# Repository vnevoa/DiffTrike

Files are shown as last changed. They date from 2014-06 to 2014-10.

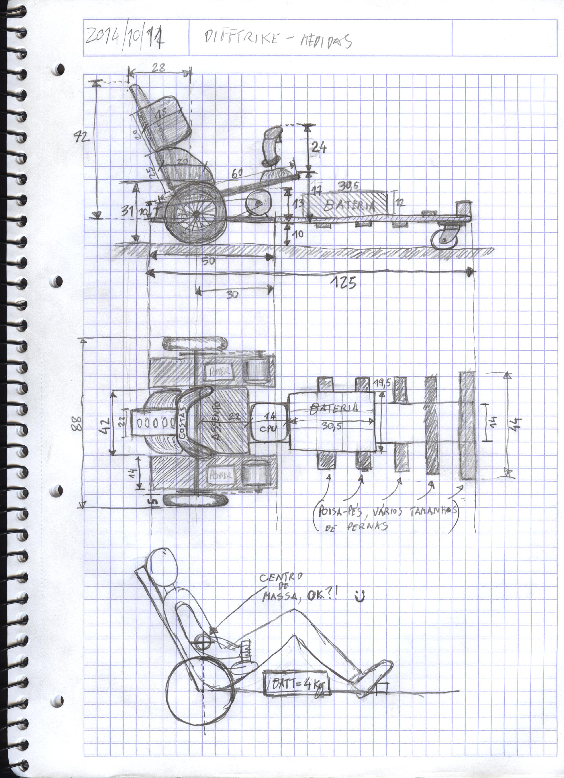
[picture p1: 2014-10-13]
Mechanical/MakerFaire Difftrike MarkIV dimensions.jpg

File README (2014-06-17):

The DiffTrike project attempts to develop the embedded control system
for a Differential Traction Hybrid Human-Electric Tricycle.

The project hosts one set of files for each hardware incarnation:
- MarkI: no files, was a purely analog solution.
- MarkII: Openmoko GTA02 controller + NJay's Homebrew Power bridges.
- MarkIII: Raspberry Pi controller + Devantech MD03 robotics power bridges.
- MarkIV: Raspberry Pi controller + NJay's Homebrew Power bridges & comms bridge.

The copyright licence of this Open Source project's files is the GNU GPL version 3.
Feel free to hack away, fork, or contribute. Just don't ask me for money for any reason whatsoever. :)

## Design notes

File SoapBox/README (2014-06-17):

This is the place for all the files that implement the SoapBox Mark IV proof-of-concept controller, in its fourth incarnation platform. Everything here is copied into the on-board controller of the Trike. 
Currently the chosen Hardware for this controller is a Raspberry Pi board, type A (use /dev/i2c-0 instead of /dev/i2c-1 on type B) plus a pair of NJay's Homebrew Power bridges.

The GNU/Linux distribution used as a basis for this controller is the Debian based "Raspbian" because it is the one suggested by the RasPi community.
You can download the latest card-flashable images from http://www.raspberrypi.org/downloads and flash them onto the SD-card by following these instructions: http://elinux.org/RPi_Easy_SD_Card_Setup

After flashing and booting it and running the built-in configuration wizard, just copy over the files to /home/pi/SoapBox/, open up a console (local or SSH) and run the install script by doing "chmod +x /home/pi/SoapBox/sbinstall.sh; sudo /home/pi/SoapBox/sbinstall.sh".

Project files and their function:
- "sbinstall.sh": the installation script for this software package into a Raspbian distro.
- "interfaces" corresponds to the /etc/network/interfaces linux configuration file.
- "soapbox.sh" is a SysV init script that launches and kills the controller application once it is installed in /etc/init.d/ and links produced with "update-rc.d soapbox.sh defaults".
- "sb.py": the control application itself, to be placed in /home/pi/SoapBox/.
- "sb_*.py": the custom modules necessary to the main application, also going into /home/pi/SoapBox/.

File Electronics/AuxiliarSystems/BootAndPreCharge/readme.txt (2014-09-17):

DiffTrike system boot and precharge auxiliar system.

Power is applied to the sub-systems by means of relays, such that power can be
enabled/disabled safely by the system controller or user.

To turn ON the trike there must be a procedure that ensures safetty, avoiding
unintended motor turn ON. And there must be a simple way for a human to quickly
turn power OFF in an emergency.

Power controllers such as motor controllers have big capacitance at the power
rails input. This capacitance needs to be charged in a controlled way to avoid
huge inrush currents which cause switch sparking and capacitor accelerated
ageing. It is the task of the precharger to slowly charge the capacitance until
it approaches the system voltage, and only then enable full power to the power
controller.

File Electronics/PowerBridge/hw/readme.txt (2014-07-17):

Here is the hardware design files for the DiffTrike h-bridge controller.
This is still work in progress, and the project is not yet totally decoupled
from my personal development environment, so you've been warned.

There are 4 boards in this project, developed with KiCAD:

 1) bridge-power
    The base board that holds the power switches (MOSFETs), DC-link capacitors,
    current sense resistors, fast current sens voltage comparator, 5V regulator
    and connectors for the controller and MOSFET driver boards.

 2) bridge-fet-drivers
    4 discreet MOSFET drivers, 2 for a N-channel and 2 for a P-channel, 24V
    power supply.

 3) bridge-ctrller
    Microcontroller and related support circuitry to control the bridge.

 4) bridge-ctrller-addon
    I2C isolation bridge, heatsink temperature sensing, motor temperature
    sensing support circuitry.

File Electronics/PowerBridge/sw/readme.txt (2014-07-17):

Here is the software for the DiffTrike h-bridge controller.
This is still work in progress, and the project is not yet totally decoupled
from my personal development environment, so you've been warned.

The software implements an I2C interface of 8 registers of 1 byte and controls
the 4 switches (currently MOSFETs) of an h-bridge by providing speed (PWM) and
reporting motor current, temperatures and bridge supply voltage.
Synchronous rectification is employed for improved efficiency over the simpler
assynchronous method.

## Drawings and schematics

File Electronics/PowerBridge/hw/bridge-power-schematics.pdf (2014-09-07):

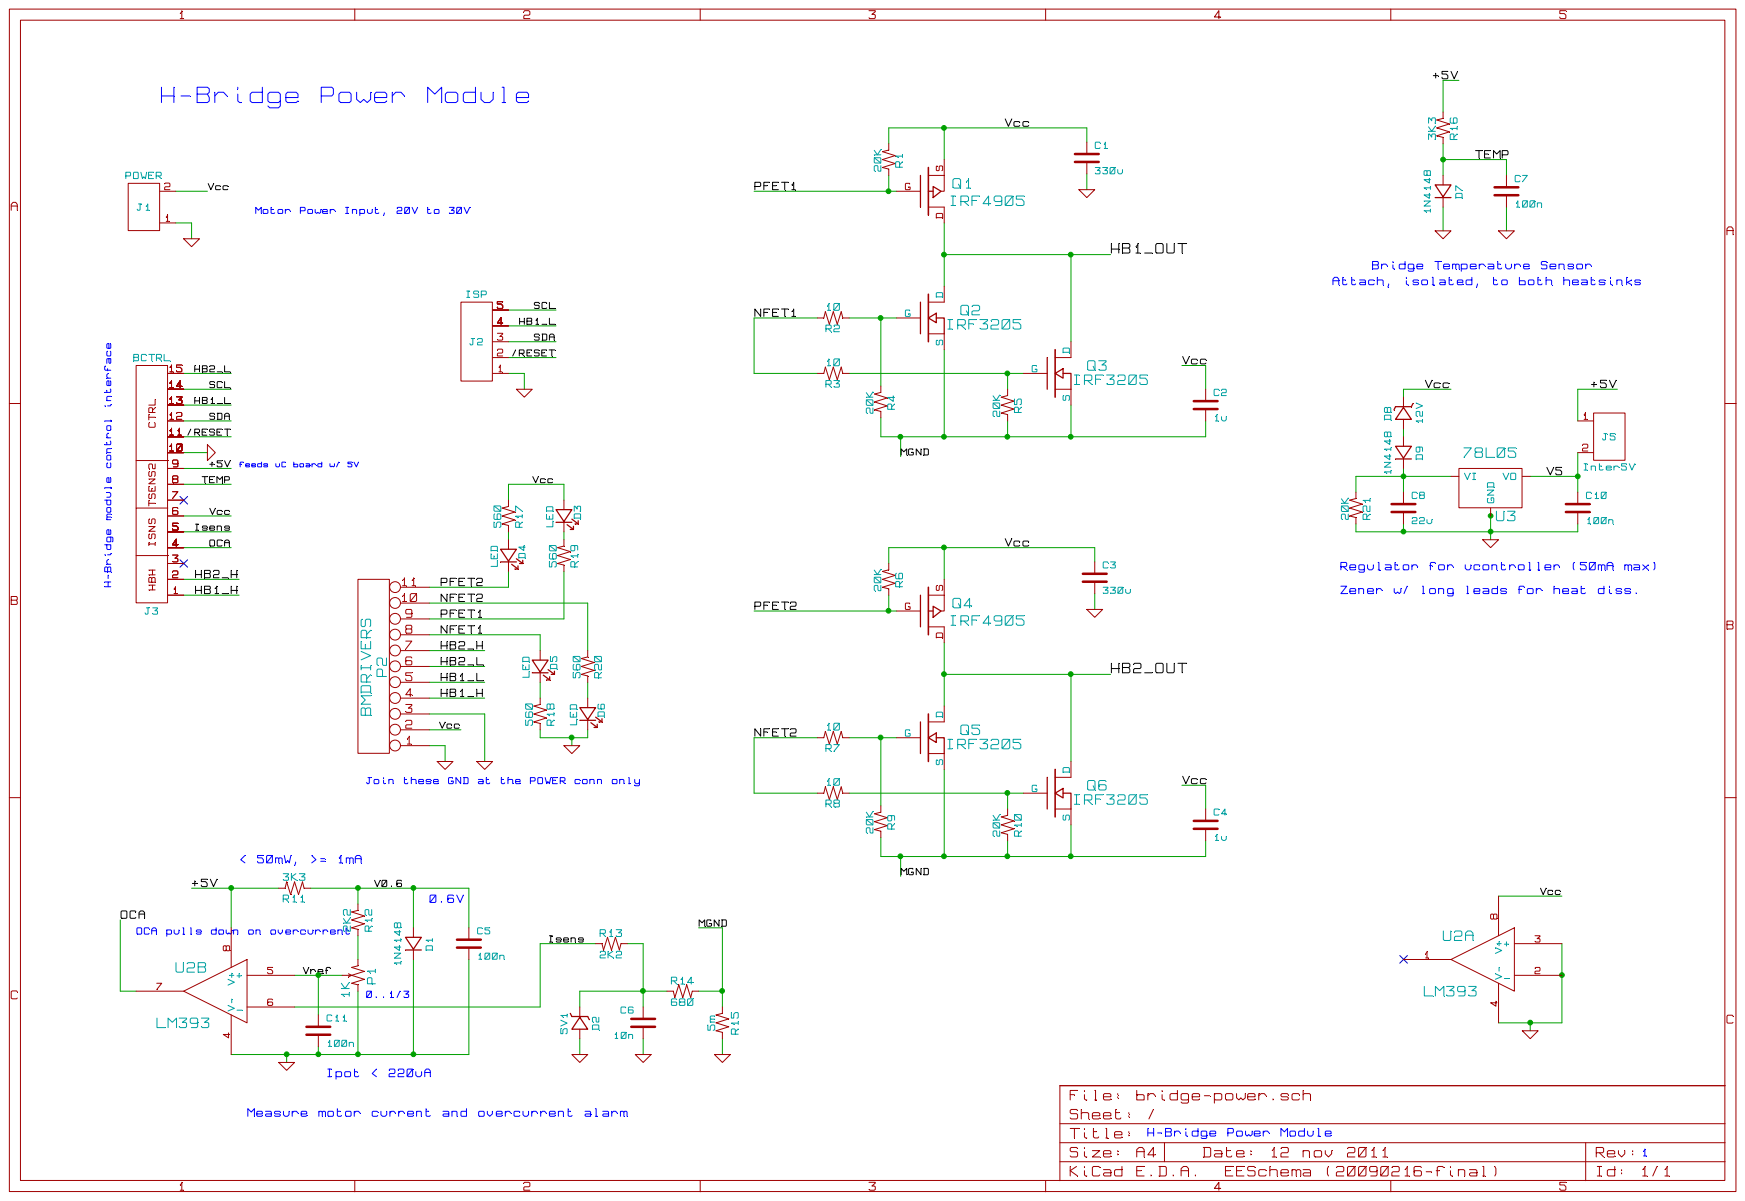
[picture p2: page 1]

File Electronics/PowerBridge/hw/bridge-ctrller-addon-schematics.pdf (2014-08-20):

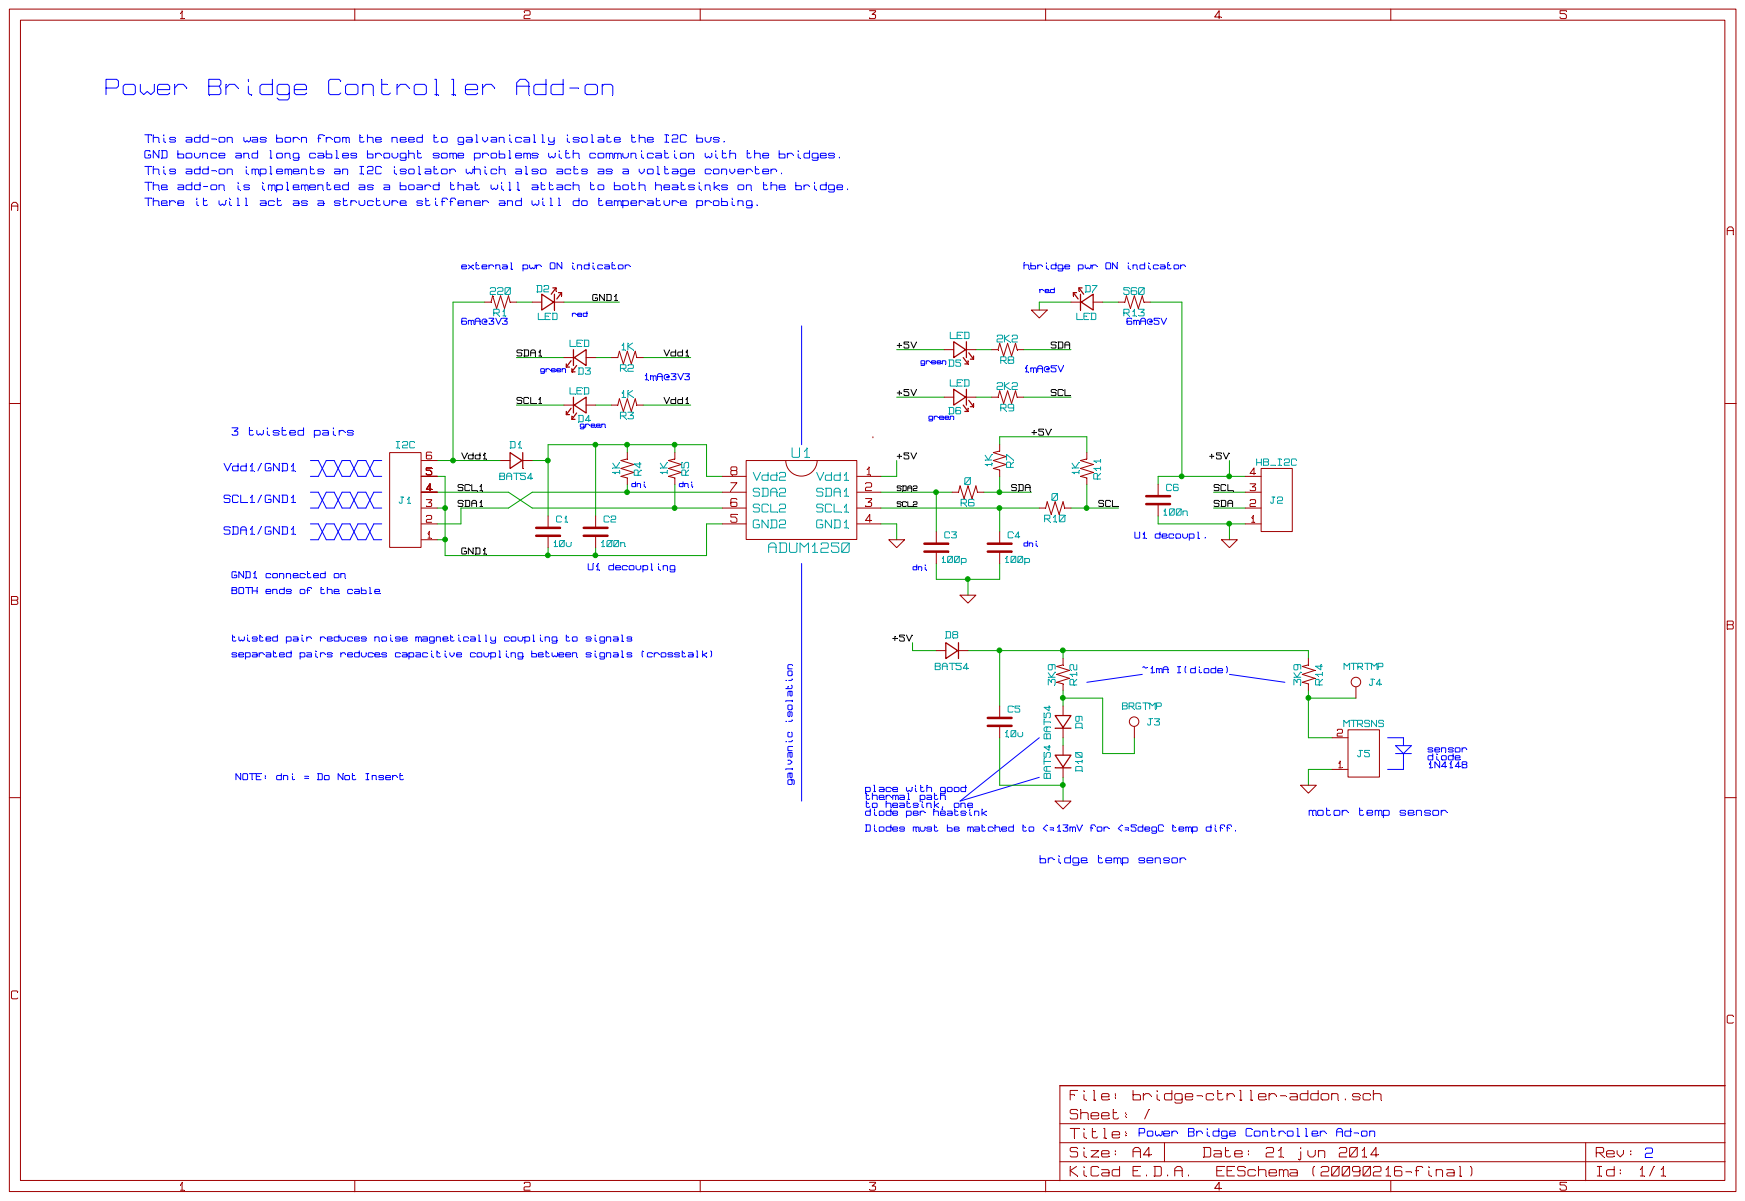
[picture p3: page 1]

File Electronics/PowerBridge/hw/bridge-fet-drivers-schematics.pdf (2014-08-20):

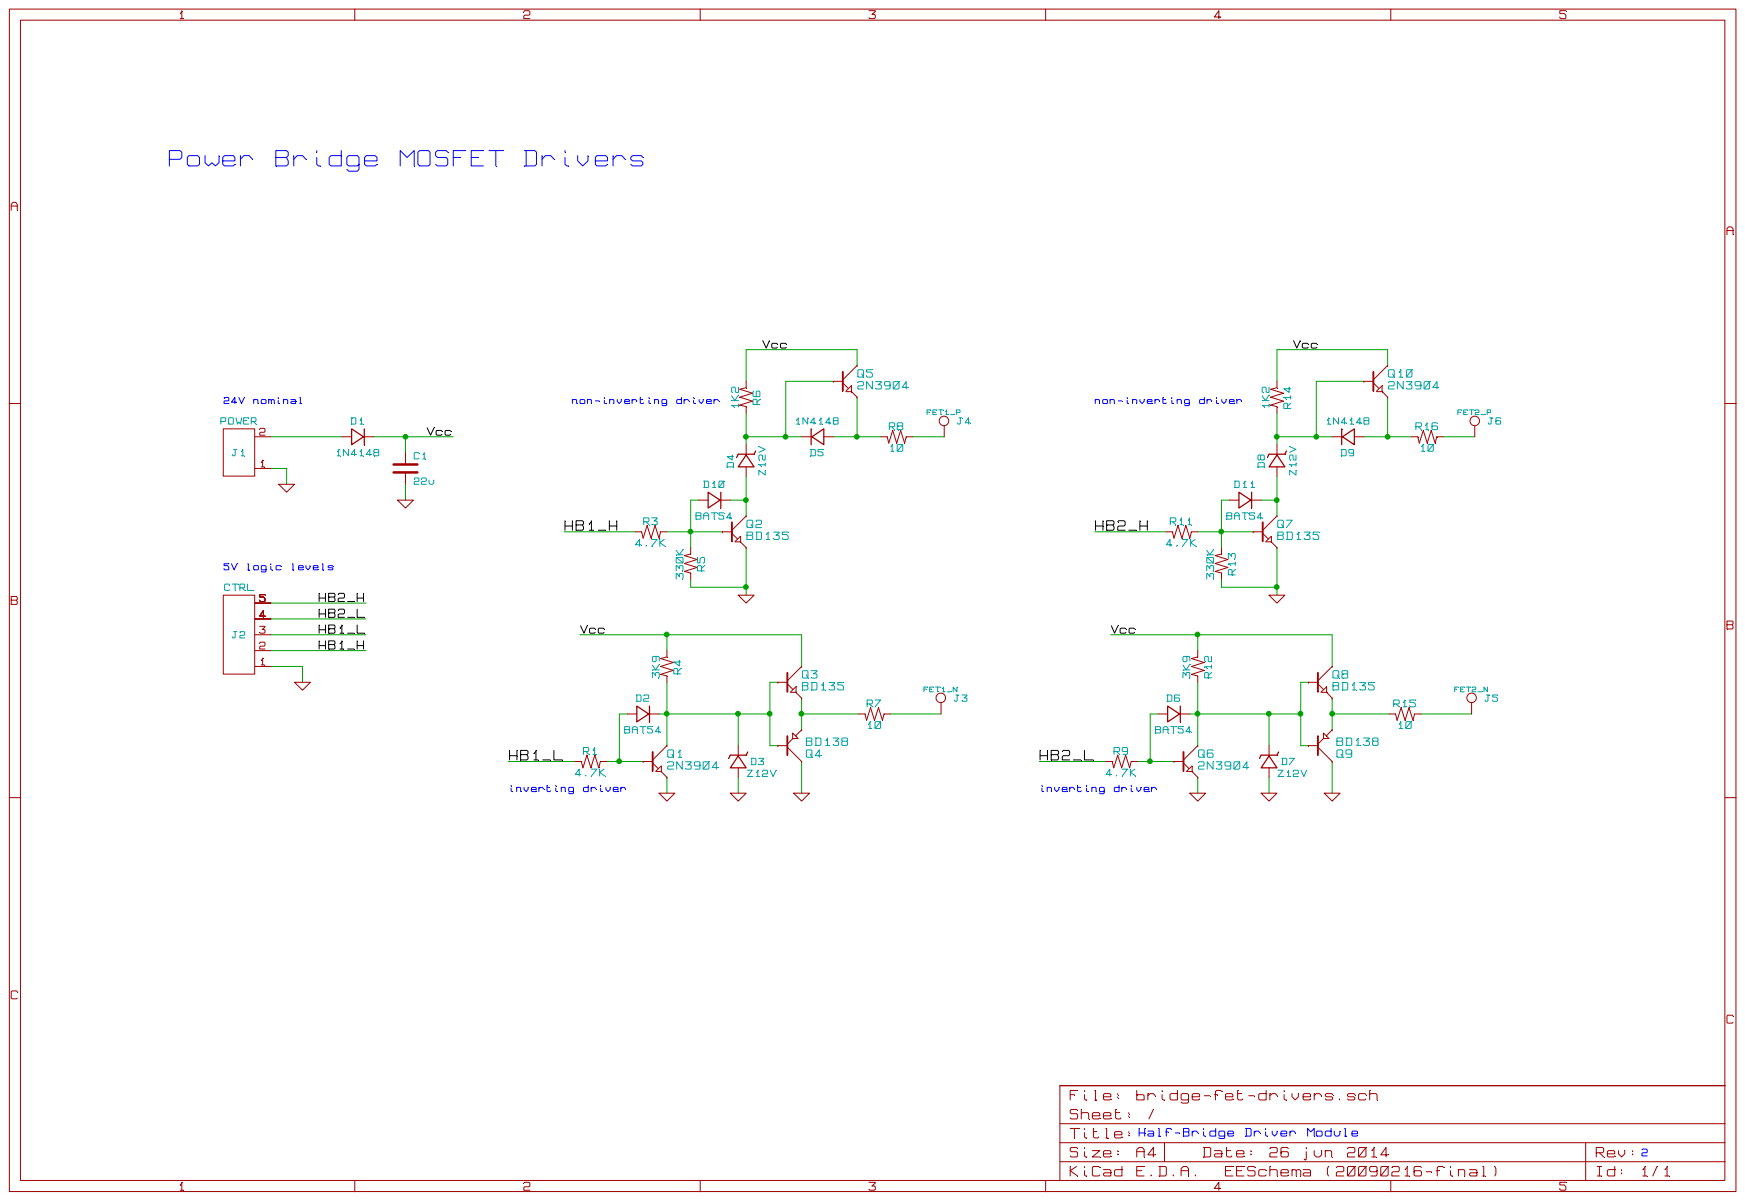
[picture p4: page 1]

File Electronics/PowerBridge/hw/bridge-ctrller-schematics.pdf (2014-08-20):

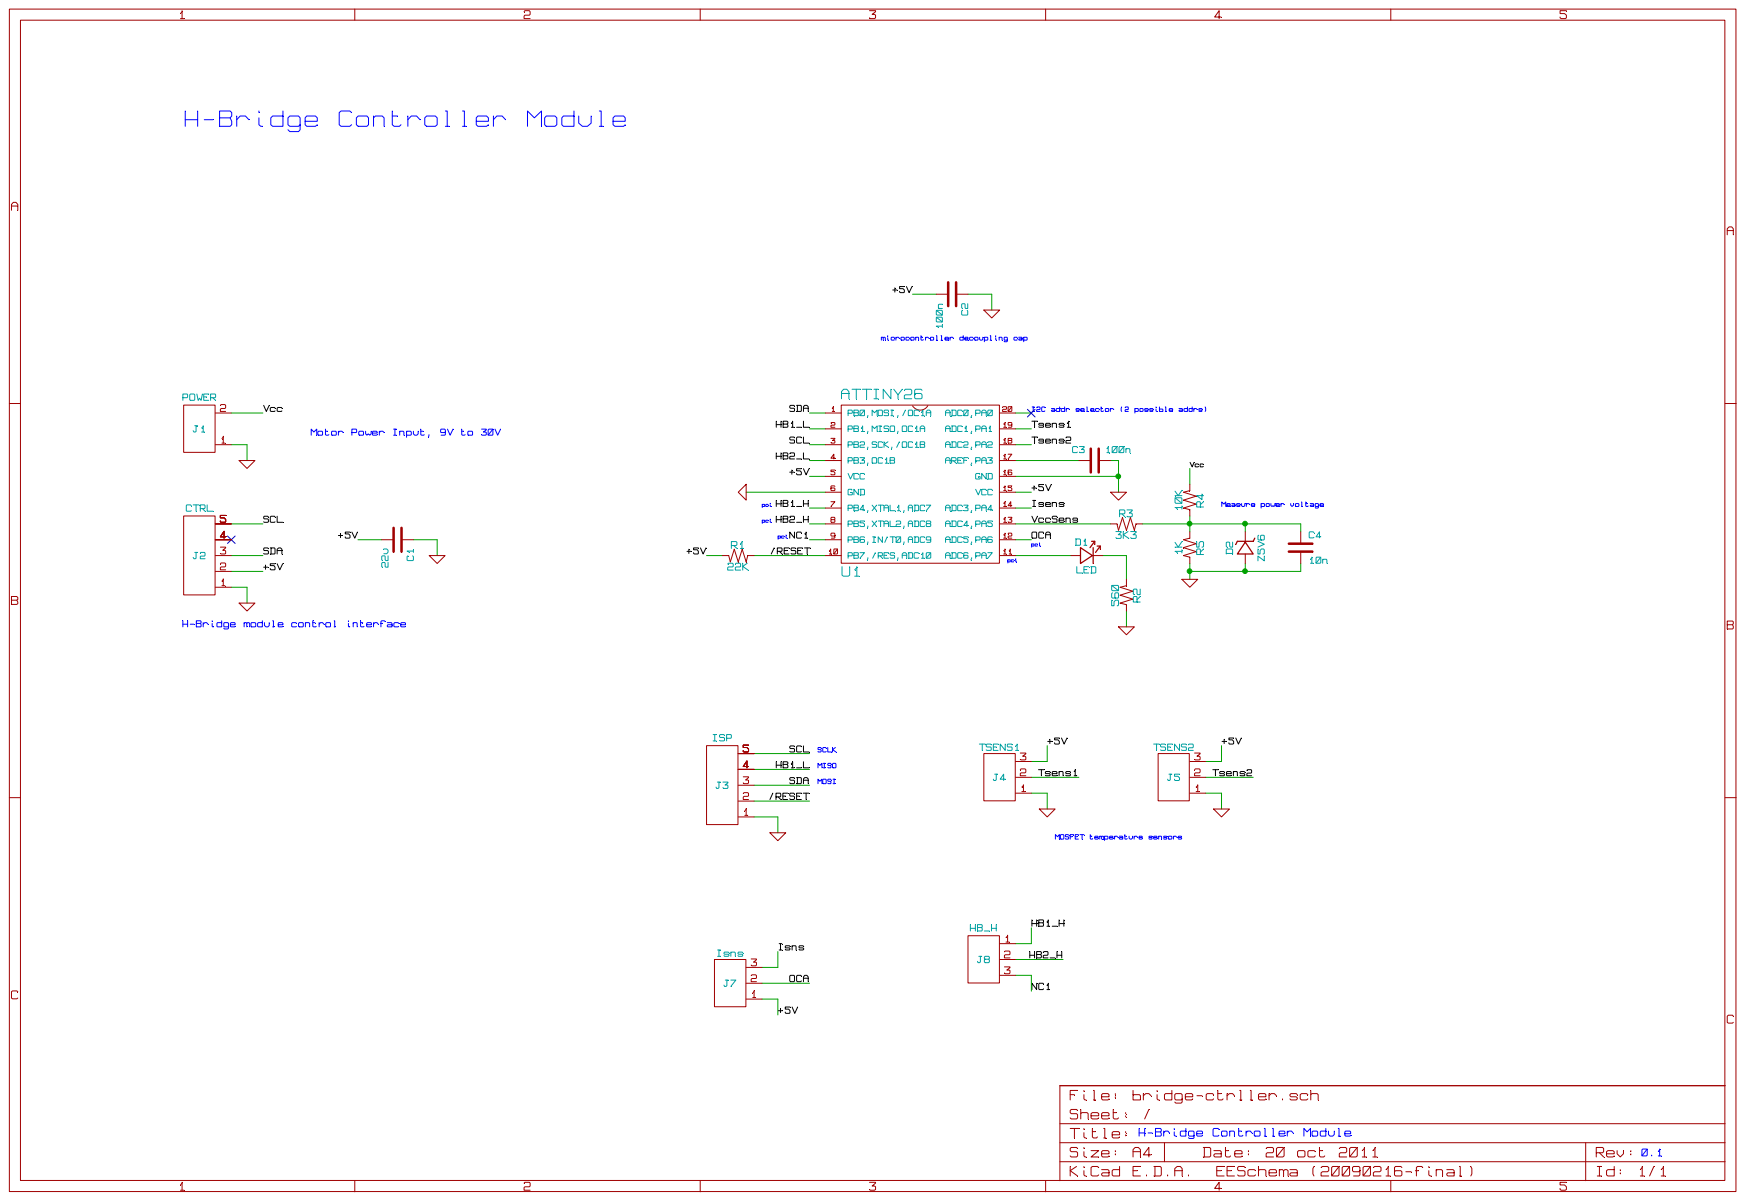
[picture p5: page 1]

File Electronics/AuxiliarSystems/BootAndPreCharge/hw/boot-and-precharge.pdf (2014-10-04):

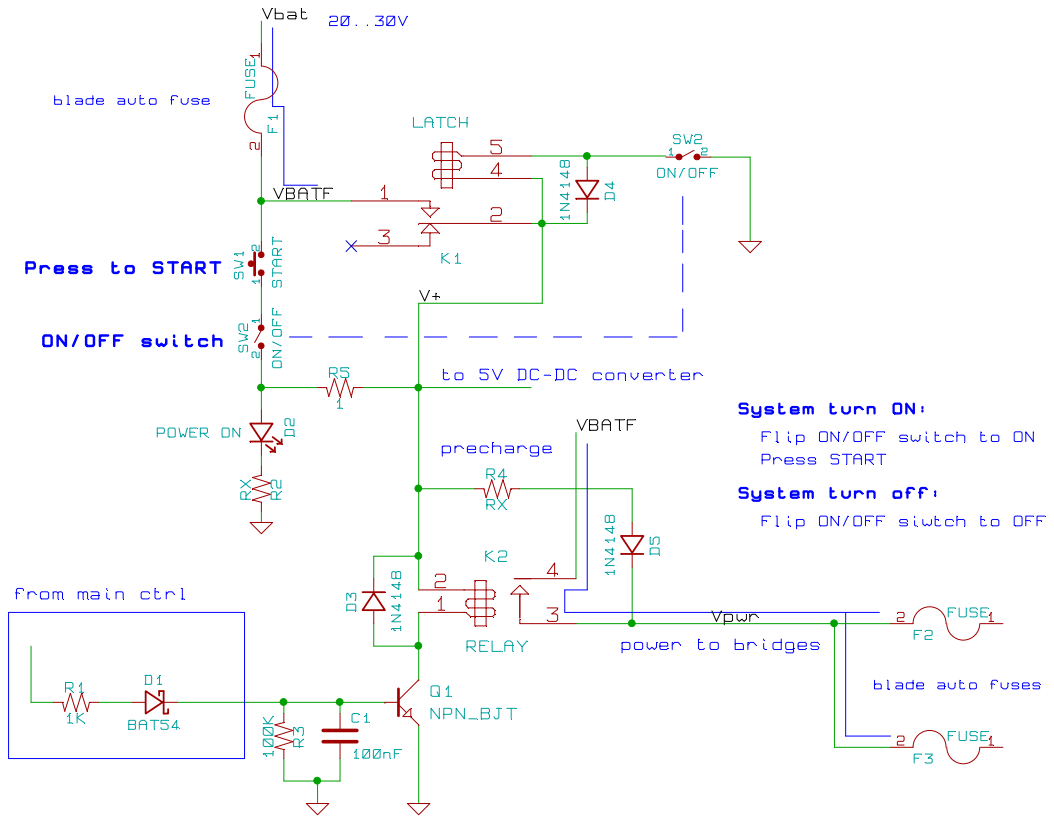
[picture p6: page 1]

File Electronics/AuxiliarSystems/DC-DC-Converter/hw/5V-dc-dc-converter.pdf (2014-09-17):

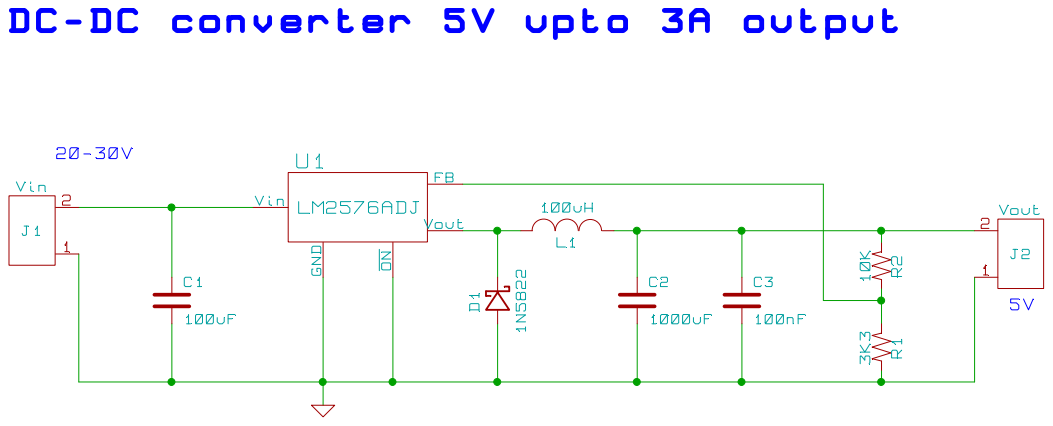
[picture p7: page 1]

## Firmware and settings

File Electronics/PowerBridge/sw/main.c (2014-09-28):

/**
 * Power H-Bridge Controller Fw
 *
 * Copyright (c) 2010-2014 Nuno João
 * http://www.EmbeddedDreams.com
 *
 * This file is part of DiffTrike.
 *
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
 * You should have received a copy of the GNU General Public License
 * along with DiffTrike. If not, see <http://www.gnu.org/licenses/>.
 */

#include <avr/io.h>
#include <avr/interrupt.h>
#include <avr/sleep.h>
#include <avr/pgmspace.h>
#include <avr/eeprom.h>
#include <util/delay.h>
#include "i2c_slave.h"


// This value can be read from one of the I2C registers
#define FW_VERSION  27


/// ---- Compilation flags BEGIN ------------

// Use this to control what to compile to run in the AVR simulator. Currently
// it disables some non-critical delays.
//#define SIMULATOR

// The output stage double pulse test mode.
//#define ENABLE_DOUBLE_PULSE

// Some compile modes need more code space, which can be obtained by dropping
// things like the ADC code.
//#define DISABLE_ADC

// Control of the OverCurrentAlarm code. Disabling it disables current
// limiting, which may toast the controller if abused.
//#define DISABLE_OCA

// Code to write the params to EEPROM is not always needed so we remove it for space.
#define DISABLE_EEPROM_WRITE

// Auto config for double pulse test mode.
#ifdef ENABLE_DOUBLE_PULSE
#   define DISABLE_ADC
#   define DISABLE_EEPROM_WRITE
#endif

/// ---- Compilation flags END --------------


#define ON      1
#define OFF     0
#define true    1
#define false   0

#define word    uint16_t
#define bool    byte

#define MIN_MOTOR_VCC           22  // V
#define MAX_CURRENT             20  // A
#define MAX_TEMPERATURE         60  //ºC

#define PWM_VALUE_HB1           OCR1A
#define PWM_VALUE_HB2           OCR1B

#define MIN_PWM     20

#define PFWMODE     ON

#define PortRead(port_letter, bits)     (PIN ## port_letter & (bits))
#define PortSet(port_letter, bits)      PORT ## port_letter |= (bits)
#define PortClear(port_letter, bits)    PORT ## port_letter &= ~(bits)
#define PortToggle(port_letter, bits)   PORT ## port_letter ^= (bits)


// AVR pin assigned functions
enum {
    eI2CaddrSel     = _BV(PA0),
    eBridgeTemp     = _BV(PA1),
    eMotorTemp      = _BV(PA2),
    ePA3            = _BV(PA3),
    eOCA            = _BV(PA4),
    eVccSense       = _BV(PA5),
    eIsense         = _BV(PA6),
    eLED            = _BV(PA7),

    eSDA            = _BV(PB0),
    eHB1_L          = _BV(PB1),     // PWM OC1A
    eSCL            = _BV(PB2),
    eHB2_L          = _BV(PB3),     // PWM OC1B
    eHB1_H          = _BV(PB4),
    eHB2_H          = _BV(PB5),
    ePB6            = _BV(PB6),
    eRESET          = _BV(PB7),
};


// ADC channels
enum {
    // goes to the add-on to be "split" into 2 sensors, 1 for each heatsink
    eADC_Temp1Bridge        = 1,
    // this goes to the power board where there's a doide connection "socket"
    eADC_Temp2Motor         = 2,
    eADC_VccSens            = 4,
    eADC_MotorDriveCurrent  = 5,

    eADC_NumOfChannels
};


// The registers we support. Can be read, some written, through I2C:
enum {
    eI2cReg_Command         = 0,    // RW  command
    // Status: b0~b3: heartbeat, b4:over-current, b5:over-temperature, b6:busy, b7:?
    eI2cReg_Status          = 1,    //  R  status
    // Speed: speed/direction:  b7: direction; b0~6: Speed
    eI2cReg_Speed           = 2,    // RW  speed
    // raw diode reading
    eI2cReg_HBridgeTemp     = 3,    //  W  controller temperature
    // raw diode reading
    eI2cReg_MotorTemp       = 4,    //  R  motor temperature
    // Motor driving current (I), x10 in A (0-25.5A)
    //  I = MotorCurrent / 10
    eI2cReg_MotorCurrent    = 5,    //  R  motor current
    // Controller's power supply voltage (Vcc), minus 10V x10 (10-29.6V)
    //  Vcc = HBridgeVcc / 10 + 10
    eI2cReg_HBridgeVcc      = 6,    //  R  controller Vcc
    eI2cReg_SwRevision      = 7,    //  R  sw revision
};

// Status register bit flags
enum {
    eStatus_HeartBeat           = _BV(0) | _BV(1) | _BV(2) | _BV(3),
    eStatus_MotorOverCurrent    = _BV(4),
    eStatus_OverTemperature     = _BV(5),       // currently not used
    eStatus_Busy                = _BV(6),       // currently not used
    eStatus_Reserved            = _BV(7),
};

// Commands for the Command Register
enum {
    // Util commands
    eCmd_Reset = 0,
    eCmd_SetI2cAddr,
    eCmd_SetVref,
    eCmd_GetVref,
    // Special bitmask config word, when cmd is written with b7 = 1
    eCmd_DisableDissipativeBreak = 0x80,
    eCmd_EnableDissipativeBreak = 0x81,
    // Debug commands
    eCmd_DoDoublePulseTest,
};


// Configuration params data structure.
typedef struct {
    byte    adcVrefx10;
    byte    i2cAddr;
} TEECfg;


// Configuration parameters.
static TEECfg  gCfg;

static byte  gCurrSpeed = 0;

static volatile word  gAdc[eADC_NumOfChannels];


// Our own sleep function. AVR libc's sleep_mode() will always enable sleep mode on
// entry and disable it on exit, which takes up 4 instructions. We need that time.
static inline void sleep (void)
{
    asm volatile("sleep");
}


static inline void OCAInterrupt (bool on)
{
#  ifndef DISABLE_OCA
    if (on)
        GIMSK |= _BV(PCIE1);
    else
        GIMSK &= ~_BV(PCIE1);
#  endif
}


static inline void SetWatchdog (bool on)
{
    if (on)
    {
        WDTCR = _BV(WDE) |      // enable watchdog
                _BV(WDP2)       // ~255ms max reset period
                ;
        asm volatile("wdr");    // watchdog reset
    }
    else
    {
        // NOTE: interrupts must be disabled, these 2 writes must be
        //       done atomically and withtin 4 clock cycles.
        WDTCR = _BV(WDCE) | _BV(WDE);
        WDTCR = 0;
    }
}


static inline void TopHB1 (bool on)
{
    if (on)
    {
        PORTB |=  eHB1_H;
    }
    else
    {
        PORTB &= ~eHB1_H;
    }
}

static inline void TopHB2 (bool on)
{
    if (on)
    {
        PORTB |=  eHB2_H;
    }
    else
    {
        PORTB &= ~eHB2_H;
    }
}

static inline void BotHB1 (bool on)
{
    // bottom drivers are inverting
    if (on)
    {
        PORTB &= ~eHB1_L;
    }
    else
    {
        PORTB |=  eHB1_L;
    }
}

static inline void BotHB2 (bool on)
{
    // bottom drivers are inverting
    if (on)
    {
        PORTB &= ~eHB2_L;
    }
    else
    {
        PORTB |=  eHB2_L;
    }
}


static void AllOff (void)
{
    // Disable interrupts Overflow, OutputCompare A and B
    TIMSK &= ~ (_BV(TOIE1) | _BV(OCIE1A) | _BV(OCIE1B));
    TopHB1(OFF);
    TopHB2(OFF);
    BotHB1(OFF);
    BotHB2(OFF);
}


static void DissipativeBreak (void)
{
    TopHB1(OFF);
    TopHB2(OFF);
    _delay_us(3);
    BotHB1(ON);
    BotHB2(ON);
}


static inline byte isFwd (void)
{
    return TIMSK & _BV(OCIE1A);
}


static inline void BkwOff (void)
{
    BotHB2(OFF);
    _delay_us(1.5);
    TopHB2(PFWMODE);
}


static inline void FwOff (void)
{
    BotHB1(OFF);
    _delay_us(1.5);
    TopHB1(PFWMODE);
}


static void clear_timer_flags (void)
{
    TIFR |= _BV(TOV1);
    TIFR |= _BV(OCF1A) | _BV(OCF1B);
}


// Note: to be invoked with interrupts disabled
static inline void GoFw (byte val)
{
    if (gCurrSpeed == 0 || !isFwd())     // is turning-on / reversing now?
    {
        DissipativeBreak();

        TIMSK = (TIMSK & ~_BV(OCIE1B)) | _BV(TOIE1) | _BV(OCIE1A);

        BotHB1(OFF);
        BotHB2(OFF);
        _delay_us(1.6);
        TopHB2(ON);

        // Make TCNT1 overflow soon. It will then start the PWM cycle,
        // turning the bottom MOSFET ON, in the overflow interrupt.
        TCNT1 = 0xf0;
        clear_timer_flags();
    }
    gCurrSpeed = val;
}


// Note: to be invoked with interrupts disabled
static inline void GoBw (byte val)
{
    if (gCurrSpeed == 0 || isFwd())     // is turning-on / reversing now?
    {
        DissipativeBreak();

        TIMSK = (TIMSK & ~_BV(OCIE1A)) | _BV(TOIE1) | _BV(OCIE1B);

        BotHB1(OFF);
        _delay_us(1.6);
        TopHB1(ON);
        BotHB2(OFF);

        // Make TCNT1 overflow soon. It will then start the PWM cycle,
        // turning the bottom MOSFET ON, in the overflow interrupt.
        TCNT1 = 0xf0;
        clear_timer_flags();
    }
    gCurrSpeed = val;
}


ISR (TIMER1_OVF1_vect)
{
#  ifndef DISABLE_OCA
    // Don't turn ON while OCA is active.
    if ((PINA & eOCA) == 0)
    {
        return;
    }
#  endif

    if (isFwd())
    {
        TopHB1(OFF);
        // Update duty cycle here, at the beginning of the PWM cycle.
        // This ensures glitch free PWM on duty cycle changes.
        // 3 cycles (0.375us @ 8MHz)
        PWM_VALUE_HB1 = gCurrSpeed;
        _delay_us(1.3 - 0.375);
        BotHB1(ON);
    }
    else
    {
        TopHB2(OFF);
        // Update duty cycle here, at the beginning of the PWM cycle.
        // This ensures glitch free PWM on duty cycle changes.
        PWM_VALUE_HB2 = gCurrSpeed;
        _delay_us(1.3 - 0.375);
        BotHB2(ON);
    }

    // We can clear the current limiting status flag, as here we know
    // we're not limiting.
    // 5 cycles (0.625us @ 8MHz)
    i2c_Set_Reg(eI2cReg_Status, i2c_Get_Reg(eI2cReg_Status) & (~eStatus_MotorOverCurrent));

    // Start the ADC to read the (motor driving) current. Result to be processed
    // on the ADC interrupt.
    if ((ADMUX & 0x0F) == eADC_MotorDriveCurrent)
        ADCSR |= _BV(ADSC);         // 2 cycles (0.25us @ 8MHz)
}


ISR (TIMER1_CMPA_vect)
{
    FwOff();
}


ISR (TIMER1_CMPB_vect)
{
    BkwOff();
}


#ifndef DISABLE_OCA
ISR(IO_PINS_vect)
{
    // We'll get also interrupts due to other pins. Filter the state we're
    // interested in, which is OCA active (= 0).
    if ((PINA & eOCA) == 0)
    {
        // End the current PWM duty ON.
        if (isFwd())
        {
            FwOff();
        }
        else
        {
            BkwOff();
        }
        // Signal OCA. Bit is reset on every PWM period start (if eOCA is inactive).
        i2c_Set_Reg(eI2cReg_Status, i2c_Get_Reg(eI2cReg_Status) | eStatus_MotorOverCurrent);
    }
}
#endif


#ifndef DISABLE_ADC
ISR(ADC_vect)
{
    word  val = ADCW;       // must be read with interrupts disabled!

    // This interrupt is slow and low priority, so release the big cpu lock :)
    sei();

    byte  admux = ADMUX;
    byte  chn = admux & 0x0F;
    admux &= 0xF0;

    switch (chn)
    {
        case eADC_MotorDriveCurrent :
        {
            ADMUX = admux | eADC_Temp1Bridge;
            gAdc[eADC_MotorDriveCurrent] = val;
            // Start next conversion.
            ADCSR |= _BV(ADSC);
            break;
        }
        case eADC_Temp1Bridge :
        {
            ADMUX = admux | eADC_Temp2Motor;
            gAdc[eADC_Temp1Bridge] = val;
            // Start next conversion.
            ADCSR |= _BV(ADSC);
            break;
        }
        case eADC_Temp2Motor :
        {
            ADMUX = admux | eADC_VccSens;
            gAdc[eADC_Temp2Motor] = val;
            // Start next conversion.
            ADCSR |= _BV(ADSC);
            break;
        }
        case eADC_VccSens :
        {
            ADMUX = admux | eADC_MotorDriveCurrent;
            gAdc[eADC_VccSens] = val;
            // Start next conversion only if the motor is running, otherwise
            // it has to be started at the beginning of the PWM period.
            if (!gCurrSpeed)
                ADCSR |= _BV(ADSC);
            break;
        }
    }
}
#endif


/**
 * ADC initialisation
 */
static void adc_init (void)
{
#  ifndef DISABLE_ADC
    ADMUX |= 0
        // Select internal 2.7V Vref with decoupling cap at AREF.
            | _BV(REFS1) | _BV(REFS0)
        // Select 1st channel to sample, motor drive current.
            | eADC_MotorDriveCurrent     // Isense
            ;

    // Fadc = 125KHz (adc-prescaler = 64 -> 8MHz / 64 = 125KHz -> 8us)
    //ADCSR |= _BV(ADPS2) | _BV(ADPS1);
    // Fadc = 250KHz (adc-prescaler = 32 -> 8MHz / 32 = 250KHz -> 4us)
    ADCSR |= _BV(ADPS2) | _BV(ADPS0);

    // Enable ADC conversion complete interrupt.
    ADCSR |= _BV(ADIE);

    // Enable ADC. It will always be enabled.
    ADCSR |= _BV(ADEN);

    // Start the 1st conversion to trigger the ADC reading process.
    ADCSR |= _BV(ADSC);
#  endif
}


/**
 * \brief Ports initialisation
 */
static void ports_init (void)
{
    // Keep in mind that this routine can be called just to re-init the ports,
    // and therefore it must not assume any initial state, and must not change
    // things it doesn't use.

    PORTB |= 0
        // H-bridge pins as outputs, starting all off.
            | (eHB1_L | eHB2_L)    // bottom MOSFETs off (inverter MOSFET driver)
        // Enable pull-ups on unused pins, to have stable inputs.
            | ePB6
        ;
        // At this point, the pull-ups are ON and we're already actively turning
        // OFF the bottom MOSFETs. Nevertheless, the bottom drivers keep the MOSFETs
        // off when not driven.
        // The top MOSFETs are OFF because the drivers are not being driven.
    DDRB  |=  (eHB1_L | eHB2_L | eHB1_H | eHB2_H);
        // Now that all pins are made outputs, the top MOSFETs are being actively
        // driven off. The bottom MOSFETs are gone from pull-up driven off to
        // actively driven off.

    AllOff();  // inits some state

    PORTA |= 0
        // Enable pull-up for base i2c address selector.
            | eI2CaddrSel       // (currently unused)
        // Enable pull-up on OCA (Over Current Alarm) pin.
            | eOCA
        // Enable pull-ups on unused pins, to have stable inputs.
            | ePA3
        ;
    // LED pin as output.
    DDRA  |= eLED;

    // Need to disable the VCOMP for the pin change interrupt to trigger on OCA's pin.
    ACSR |= _BV(ACD);
}


static void pwm_init (void)
{
    // Counter only works as a counter.
    TCCR1A = 0;
    // Overflow happens at (sysclock / prescaler / (OCRC + 1))
    // Prescaler: 1: /1, 2: /2, 3: /4, 4: /8
    // Ctr overflow freq: 8MHz / 2 / (255 + 1) = 15.625KHz  (2)
    //                    8MHz / 4 / (255 + 1) =  7.813KHz  (3)
    //                    8MHz / 4 / (249 + 1) =  8.000KHz  (3)
    //                    8MHz / 4 / (199 + 1) = 10.000KHz  (3)
    TCCR1B = (TCCR1B & 0xF0) | 3;
    OCR1C = 0xFF;
}


byte volatile gI2C_RegFile[I2C_REGISTER_FILE_SIZE];


static void twi_init (void)
{
    i2c_Set_Reg(eI2cReg_SwRevision, FW_VERSION);

    i2c_Set_Reg_Access(eI2cReg_Command, eI2c_RW);
    i2c_Set_Reg_Access(eI2cReg_Speed, eI2c_RW);
#  if !defined(DISABLE_EEPROM_WRITE)||defined(ENABLE_DOUBLE_PULSE)
    // (writing to this reg is used as a parameter for some functionality)
    i2c_Set_Reg_Access(eI2cReg_MotorCurrent, eI2c_RW);
#  endif

    i2c_Slave_Initialise(gCfg.i2cAddr);
}


static byte CalcChecksum (void* ptr, byte size)
{
    byte  chksum = 0;
    while (size > 0)
    {
        size--;
        chksum += ((byte*)ptr)[size];
    }
    return chksum;
}


// EEPROM start addr of the config
#define EepromCfgAddr   3
// 1st byte of the config must be this magic number :)
#define EEPROM_MAGIC_NUMBER  0x69


#ifndef DISABLE_EEPROM_WRITE
static void SaveCfgToEeprom (void)
{
    byte  prevSREG = SREG;
    cli();
    eeprom_busy_wait();
    eeprom_write_byte((byte*)EepromCfgAddr, EEPROM_MAGIC_NUMBER);
    eeprom_busy_wait();
    eeprom_write_block(&gCfg, (byte*)(EepromCfgAddr + 1), sizeof(gCfg));
    eeprom_busy_wait();
    eeprom_write_byte((byte*)(EepromCfgAddr + 1 + sizeof(gCfg)),
                      CalcChecksum(&gCfg, sizeof(gCfg)));
    SREG = prevSREG;
}
#endif


// Read config data from the EEPROM.
// If unable to read config (no config, corrupted, etc) use a default config
// and return 0, otherwise 1.
static byte ReadCfgFromEeprom (void)
{
    byte  magic = eeprom_read_byte((byte*)EepromCfgAddr);
    if (magic == EEPROM_MAGIC_NUMBER)
    {
        eeprom_read_block(&gCfg, (byte*)(EepromCfgAddr + 1), sizeof(gCfg));
        byte  stored_chksum = eeprom_read_byte((byte*)(EepromCfgAddr + 1 + sizeof(gCfg)));
        if (CalcChecksum(&gCfg, sizeof(gCfg)) == stored_chksum)
        {
            return 1;     // success
        }
    }
    // Else set a default config.

    // This i2c addr is reserved for the default config.
    gCfg.i2cAddr = 0x20;
    gCfg.adcVrefx10 = 28;

#  ifndef DISABLE_EEPROM_WRITE
    SaveCfgToEeprom();
#  endif
    return 0;
}


static void UpdateSpeed (void)
{
    byte  speed = i2c_Get_Reg(eI2cReg_Speed);
    // Bit 7 is direction, remaining bits are half speed.
    byte  dir = speed & 0x80;
    speed <<= 1;

    byte  prevSREG = SREG;
    cli();

    if (speed == 0)
    {
        SetWatchdog(OFF);
        OCAInterrupt(OFF);
        AllOff();
        gCurrSpeed = 0;
        i2c_Set_Reg(eI2cReg_MotorCurrent, 0);
        i2c_Set_Reg(eI2cReg_Status, 0);
        // Make sure the ADC readings don't stop, triggering one.
        ADCSR |= _BV(ADSC);
    }
    else
    {
        // Speed has a limited range in both ends.
        if (speed < MIN_PWM)
            speed = MIN_PWM;
        if (speed > 255 - MIN_PWM)
            speed = 255 - MIN_PWM;

        if (dir == 0)
            GoFw(speed);
        else
            GoBw(speed);

        OCAInterrupt(ON);
        SetWatchdog(ON);
    }
    SREG = prevSREG;
}


/**
 * \brief Main loop
 */
int __attribute__((noreturn)) main(void)
{
    // Init the I/O ports as they control critical things and we must set
    // defined values ASAP.
    ports_init();

    // Load config params from EEPROM
    (void)ReadCfgFromEeprom();

    pwm_init();
    // Init i2c slave interface (do it while interrupts are disabled)
    twi_init();
    adc_init();

#  ifdef SIMULATOR
    i = MIN_PWM;
    i2c_Set_Reg(eI2cReg_Speed, i);
    GoFw(i);
#  endif

#  ifdef ENABLE_DOUBLE_PULSE
    // More user friendly start values
    i2c_Set_Reg(eI2cReg_Command, eCmd_DoDoublePulseTest);   // DP test cmd nr.
    i2c_Set_Reg(eI2cReg_Speed, 50);                         // 1st pulse len (us)
    i2c_Set_Reg(eI2cReg_MotorCurrent, 10);                  // pause len (us)
#  endif

    // Enable interrupts
    sei();

#  ifndef DISABLE_ADC
    word  motor_current_acc = 0;
    byte  num_motor_current_samples = 0;
#  endif

    while(1)
    {
        // Handle I2C commands
        byte  chg_mask = i2c_Get_Changed_Mask();
        if (chg_mask)
        {
            if (chg_mask & _BV(eI2cReg_Command))        // Command register
            {
                byte  cmdVal = 0x80;
                byte  cmd = i2c_Get_Reg(eI2cReg_Command);

                switch (cmd)
                {
                    // Util Commands //

                    case eCmd_Reset :
                        ports_init();
                        i2c_Set_Reg(eI2cReg_Speed, 0);
                        i2c_Set_Reg(eI2cReg_MotorCurrent, 0);
                        i2c_Set_Reg(eI2cReg_Status, 0);

                        cmdVal = 69;  // confirmation value
                        break;

#                  ifndef DISABLE_EEPROM_WRITE
                    case eCmd_SetI2cAddr :
                    {
                        byte  i2c_addr = i2c_Get_Reg(eI2cReg_MotorCurrent);
                        if (i2c_addr >= 0x20 && i2c_addr <= 0x28)
                        {
                            gCfg.i2cAddr = i2c_addr;
                            SaveCfgToEeprom();
                            cmdVal = i2c_addr;  // confirmation value
                        }
                        break;
                    }

                    case eCmd_SetVref :
                    {
                        byte  vrefx10 = i2c_Get_Reg(eI2cReg_MotorCurrent);
                        //if (gCurrAcc >= 22 && gCurrAcc <= 32)
                        {
                            gCfg.adcVrefx10 = vrefx10;
                            SaveCfgToEeprom();
                            cmdVal = vrefx10;  // confirmation value
                        }
                        break;
                    }
#                  endif

                    case eCmd_GetVref :
                        cmdVal = gCfg.adcVrefx10;
                        break;

                    // Debug Commands //
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

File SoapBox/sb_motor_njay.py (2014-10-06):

#
#    Copyright 2011 Vasco Nevoa.
#
#    This file is part of DiffTrike.
#
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
#
# This module implements the electric motor driver and data extraction.
#

import struct, time, thread
import i2c_lib

# Bridge controller registers:
REG_COMMAND = 0       #RW, Special functions, see comments below.
REG_STATUS = 1        #RO, b0~b3: heartbeat, b4:over-current, b5:over-temperature, b6:busy, b7:?
REG_PWM = 2           #RW, b7: direction; b0~6: Speed [0, 10..117]
REG_BRIDGETEMP = 3    #RO, controller temperature, raw diode reading, inversely proportional [?]
REG_MOTORTEMP = 4     #RO, motor temperature, raw diode reading, inversely proportional [?]
REG_CURRENT = 5       #RO, motoring current, Real = Read / 10 [A]
REG_BATTVOLTAGE = 6   #RO, controller's power supply voltage, Real = Read / 10 + 10 [V]
REG_FW_VERSION = 7    #RO, firmware version
# REG_COMMAND available commands:
# eCmd_Reset = 0: Turn off all FETs and reinitialize controller pins.
# eCmd_SetI2cAddr = 1: Write I2C address (in REG_CURRENT) to EEPROM (#ifnotdef DISABLE_EEPROM_WRITE)
# eCmd_SetVref = 2: Write ADC Vref (REG_CURRENT * 10) in EEPROM (#ifnotdef DISABLE_EEPROM_WRITE)
# eCmd_GetVref = 3: Get ADC Vref from EEPROM
# eCmd_DoDoublePulseTest = 4: "Double Pulse", REG_PWM = length of 1st pulse [us], REG_CURRENT = length of pause [us] (#ifdef ENABLE_DOUBLE_PULSE)

MAX_PWM = 117.0

class I2CMotorBridge():

	def __init__(self, name, filename, address, debug=False):

		self.busy = False	# microprocessor busy
		self.alarm_I = False	# overcurrent alarm
		self.alarm_T = False	# overtemperature alarm
		self.i2c_ops = 0	# i/o total count
		self.blockings = 0	# i/o fail count
		self.I = 0.0		# current Motoring current :)
		self.T = 0.0		# current Bridge temperature
		self.mT = 0.0		# current Motor temperature
		self.V = 0.0		# current Battery voltage
		self.power = 0.0	# desired power from application
		self.last_pwm = 0	# last effectively written PWM value
		self.device = i2c_lib.I2CSlave(name, filename, address)
		self.ongoing = False	# i/o thread lifespan control
		self.reset = False	# did the bridge reset?
		self.resets = 0		# how many times did the bridge reset?
		self.name = name	# friendly name
		self.debug = debug	# should I speak loudly?
		self.shorted = False # are we short-circuiting the motor?

		if self.test():
			self.ongoing = True
			thread.start_new_thread(self.ioPump, ())
		else:
			print "Device initialization failed. [%s]" % self.device.getId()


	def __del__(self):
		if self.ongoing: time.sleep(0.30)


	def test(self):
		try:
			t0 = time.time()
			self.refreshStatus()
			t1 = time.time()
			if self.debug: print "Firmware revision = %d, Read takes %0.1fms" % (self.fw, 1000*(t1-t0))
			return True
		except:
			return False


	def ioPump(self):

		t0 = time.time()
		self.i2c_ops = 0
		busy = 0
		clip = 0
		temp = 0
		self.resets = 0
		self.shorts = 0
		max_I = 0.0
		min_V = 100.0

		while self.ongoing:


			# GET status:
			try:
				self.refreshStatus()
				self.blockings = 0
				if self.busy: busy += 1
				if self.alarm_I: clip += 1
				if self.alarm_T: temp += 1
				if self.reset: self.resets += 1
				if self.I > max_I: max_I = self.I
				if self.V < min_V: min_V = self.V
			except:
				self.blockings += 1
			# count all read attempts
			self.i2c_ops += 1

			# SET behavior:
			try:
				self.writePower()
				self.blockings = 0
			except:
				self.blockings += 1
			# count all write attempts
			self.i2c_ops += 1

			# PRINT cycle:
			if self.debug:
				t1 = time.time()
				if ((t1 - t0) * 1000) > 1000:
					t0 = t1
					line = "%s:\n  %d ios;  %3.3f%% fail;" % (self.device.getId(), self.i2c_ops, 100.0*self.blockings/self.i2c_ops)
					line += "  pwm = %d%%;" % (self.power * 100.0)
					if self.shorts > 0 :
						line += " SCs = %d; " % self.shorts
					line += "  max curr = %2.1f A;" % max_I
					line += "  min volt = %2.1f V;" % min_V
					if clip: line += "  CLIP = %d;" % clip
					if self.resets: line += "  RESETS = %d;" % self.resets
					print line + "\n"
					clip = 0
					self.resets = 0
					self.shorts = 0
					max_I = 0.0
					min_V = 100.0

			# SLEEP:
			time.sleep(0.050) # 50ms -> 20 loops per second
			# exit if we fail I/O for 0.1s (10 = 5 R + 5 W)
			#if self.blockings > 10 :
			#	self.ongoing = False



	def refreshStatus(self):

		(a, b, c, d, e, f, g, h) = self.getRawData()
		#print "%s %2x %2x %2x %2x %2x %2x %2x %2x" % (self.name, a, b, c, d, e, f, g, h)
		if h != 27: # counts as a glitch
			raise Exception("I2C garbage!")
		# bridge forgot my order?
		self.reset = (c != self.last_pwm)
		# b = REG_STATUS
		self.alarm_I = b & 0x10  # b4: current limited
		# d = REG_BRIDGETEMP
		self.T = (255.0 - d) # ???
		# e = REG_MOTORTEMP
		self.mT = (255.0 - e) # ???
		# f = REG_CURRENT
		self.I = f / 10.0 # Amp
		# g = REG_BATTVOLTAGE
		self.V = g / 10.0 + 10 # Volt
		# h = REG_FW_VERSION
		self.fw = h # firmware revision


	def getCurrent(self):
		return self.I # Ampere


	def getTemperature(self):
		return self.T # Celsius


	def getMotorTemperature(self):
		return self.mT # Celsius


	def getVoltage(self):
		return self.V # Volt


	def setPower(self, desired): # [-1..1]
		self.power = max(desired, -1.0)
		self.power = min(desired, 1.0)


	def getRawData(self):
		self.device.seek(0) # seek to beginning of registers.
		data = self.device.read(8)
		return struct.unpack('BBBBBBBB', data) # dump all of them.


	def writePower(self):
		# if the IO pump stops, throw the towel.
		if not self.ongoing : 
			raise Exception("No I/O pump!")
		if abs(self.power) > 0.08:
			# if power > 8%, we are motoring:
			self.last_pwm = int(abs(self.power) * MAX_PWM)
			if self.shorted : 
				self.device.write(REG_COMMAND, 0x7F, 0x80) # turn off braking
				self.shorted = False
			if self.power < 0 : self.last_pwm |= 0x80 # reverse direction
			inv = int(0xFF & ~self.last_pwm) # binary complement as check
			self.device.write(REG_PWM, inv, self.last_pwm)
		else:
			# if power < 8%, we are braking or curving:
			# toggle short-circuiting = regenerative braking
			if not self.shorted : 
				self.device.write(REG_COMMAND, 0x7E, 0x81) # turn on braking -> motor is brake, heats up
				self.shorted = True
				self.shorts += 1
			else:
				self.device.write(REG_COMMAND, 0x7F, 0x80) # turn off braking -> motor is generator, heats up, battery charges
				self.shorted = False


# This is a simple test routine that only runs if this module is 
# called directly with "python sb_motor_md03.py"
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

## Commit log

2011-02-02 Placeholders for on-board and off-board files.
2011-02-09 reduced control loop jitter
2011-02-12 faster loop. renamed vars. sending loop time. corrected torque output limits.
2011-02-12 added timing histograms. added torque graphbars. better synchronization with server. removed generators. some pythonization.
2011-03-02 added a dummy driver for the motor bridges.
2011-04-25 Real implementation for the I2C power bridge.
2011-04-25 Integrated real device driver classes for Accelerometers and I2C Power Bridges. Initial attempt at a fail-safe robust system.
2011-04-25 New implementation of an Accelerometer device driver class. Work in progress.
2011-04-25 Added accelerometer tuning.
2011-05-10 Refactored input and output data into separate modules. Cleaned up code. Integrated data collecting devices.
2011-05-18 Added accelerometer and torque feedback graphs, as well as a testing mode.
2011-07-13 New I2C library; Changed I2C usage ^Cd testing.
2011-07-13 Temporary state to allow I2C testing.
2012-03-22 Added unit test and better buttons function.
2012-03-22 Enabled USB power.
2012-03-25 Added I2C timeout
2012-03-31 PWM should display even if no bridges.
2014-06-17 Added the Mark III files for the Raspberry Pi controller.
2014-06-18 Last developments from the lab: Better debugging and tolerance of bridge resets; Activated Dead Man's Switch on the joystick; New Restart option for Daemon; Bug fixing.
2014-07-17 Added electronics related files.
    Renamed NJAY directory to Electronics and added the current hw
    and sw state of the power h-bridge for motor control.
    [bridge-ctrller-addon.brd, bridge-ctrller-addon.sch, bridge-ctrller.brd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]
2014-07-17 Electronics/PowerBridge: Added readme files and started to decouple the hw and sw projects from my personnal development environment.
2014-07-18 Implemented motor current measurement method of waiting for the right time to start the ADC.
    Gives some results but it's not yet very reliable.
    Also more makefile cleanup.
    [bridge-ctrller.sch]
2014-07-19 Bridge Ctrller sw: Added current control, adjusted dead times and many code space optimizations.
2014-08-20 More proj decouple of dev's environment, PDF schematics and hw/sw fixes.
    KiCAD .lib files were added to the repo, hopefully they will allow to see
    the schematics on KiCAD installations without my private libs.
    Also added PDF versions of the schematics, always usefull for a quick look.
    The I2C sw module was enabling the interrupts on its initialization routine.
    Some component values were changed to reflect actual hardware. Implemented
    some fixes on the bridge-ctrller-addon after assembly and testing of
    prototypes.
    [bridge-ctrller-addon.brd, bridge-ctrller-addon.sch, bridge-fet-drivers.sch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]
2014-08-20 Hw files cleanup, minor bug removal and added PCB not-up-to-date warnings.
    Ctrller add-on: fixed wrong motor temp diode orientation and text typos.
    FET drivers: added warning on PCB that it is not 100% compliant with
    schematics.
    Fixed text typos on other files.
    [bridge-ctrller-addon.sch, bridge-fet-drivers.brd, bridge-fet-drivers.sch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]
2014-08-22 Added a double-pulse test mode, more compile options, cleanup.
    The double pulse test is a short test that allows us to see the
    switching behaviour of the power stage. The 1st pulse lets current
    build up in a stalled motor (or equivalent inductor) and then a
    second pulse ends the test. The switch off of the 1st pulse and the
    switch on of the second pulse are the relevant parts of the test,
    it's where the built-up current is switched on-off.
    Added macros to control inclusion of several feature in the compilation
    (such as the ADC and the OCA), n order to allow code space for other
    functionality such as the double-pulse test.
    [main.c]
2014-08-22 New attempt at measuring motor (driving) current.
    Current change during the PWM period should be marginal (ripple),
    typically <5%, should never be >10%. Therefore we can relax the
    requirements and sample the current shunt at the beggining of the
    ON period instead of at the end, thus making it so much easier.
    Works decently, oscilates too much at very low currents (no load
    on motor) and oscilates a little when the bridge is doing current
    limiting, but I think it's reasonable now. It's reporting about
    0.5-1A too much but that's perfectly fine.
    The current shunt filter was changed, the resistor was reduced
    from 2K2 to 680Ohm. The original values were low-passing too much,
    attenuating the signa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
    [bridge-ctrller.brd, bridge-ctrller.sch, bridge-power.sch]
2014-08-22 Fw i2c: minor optimizations and start condition interrupt infinite loop prevention.
    [i2c_slave.c]
2014-08-23 I2C register file changes.
    Droped acceleration register replacing it by another temperature register.
    Speed register now uses bit 7 for direction, bits 0-6 for speed.
2014-08-23 ADC needs to be triggered the 1st time and when the motor is off.
2014-08-23 Another ADC re-trigger fix and adaptation of EEPROM write code to the new register file.
    [main.c]
2014-08-24 Shunt filter cap back on 10nF and fixed FW special compilation modes.
    [bridge-power.sch]
2014-09-03 Updated motor module to work with latest Njay power bridge. Comms are up. WIP
2014-09-07 Updated Power module PDF schematics.
2014-09-16 Bridge Ctrller sw: v26, security features (i2c write check, system master loss detection [still disabled]) and fast boot.
    To reliability, the i2c register writes were changed to take 2 register
    values, one the bitwise complement of the other. The bridge sw only updates
    the register if so is true.
    Code for detection of system master communication was added and compiles
    but is disabled until tests can be done. This intents to detect loss of
    master while the motor is running, and gracefully turn the motor off. From
    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
2014-09-16 Made the SoapBox software comptible with version 26 of NJay's Power Bridge firmware. Added support for the Check byte on register Writes, and also a basic unit test.
2014-09-17 Electronics: Added 1st version schematics of boot and precharge auxiliar systems.
    [boot-and-precharge.sch]
2014-09-17 Bridge Ctrller sw: fix i2c module comment.
    [i2c_slave.c]
2014-09-17 Electronics: Added 1st version schematics of 5V DC-DC converter auxiliar system. WIP.
    [5V-dc-dc-converter.sch]
2014-09-17 Electronics: added DC-DC converter PDF schematics and updated sub-system name.
    [5V-dc-dc-converter.sch]
2014-09-27 Added safety feature to disable motor if i2c master is gone.
    When motor is ON (Speed register not 0 nor 0x80), the i2c
    master must re-write the register at least once every 255ms
    (nominal), otherwise the bridge controller will reset,
    freewheeling the motor.
    [main.c]
2014-09-27 Bridge Ctrller sw: Added dissipative break mode (untested).
    The command register can be written with 0x81 to enable dissipative
    breaking (using the lower FETs); if motor spinning, current speed is
    saved.
    If written with 0x80, dissipative breaking is turned off and saved speed
    is set.
    Reading the command register will return 0x80/0x81 if one of these
    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
2014-09-28 Bridge Ctrller sw: fix issue with entering dissipative break mode.
    Although the DissipativeBreak() function does all is necessary to update
    the FETs state for this mode, more state needed update when setting Speed
    to zero, specifically, UpdateSpeed() must be called as it enables/disables
    several features and updates some variables.
    [main.c]
2014-09-29 Local JS overrides remote JS; X axis expon. dampening; Fix comments.
2014-10-04 BootAndPreCharge: Fixed issue with ON/OFF switch.
    [boot-and-precharge.sch]

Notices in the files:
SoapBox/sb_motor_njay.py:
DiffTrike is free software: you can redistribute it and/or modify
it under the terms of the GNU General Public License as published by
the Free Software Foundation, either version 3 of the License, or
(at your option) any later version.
